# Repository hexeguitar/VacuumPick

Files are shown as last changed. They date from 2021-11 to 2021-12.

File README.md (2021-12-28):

# VacuumPick
### DIY vacuum pick up project for hand SMT assembly. 
The hardware is based around an inexpensive air pump, 3 valves and a controller board utilizing the ATTINY806 microcontroller.  
Firmware is available as PlatformIO project (sources) and a precompiled hex file.  
The enclosure and the handle was reused from a damaged Ayoue932 vacuum pick up.

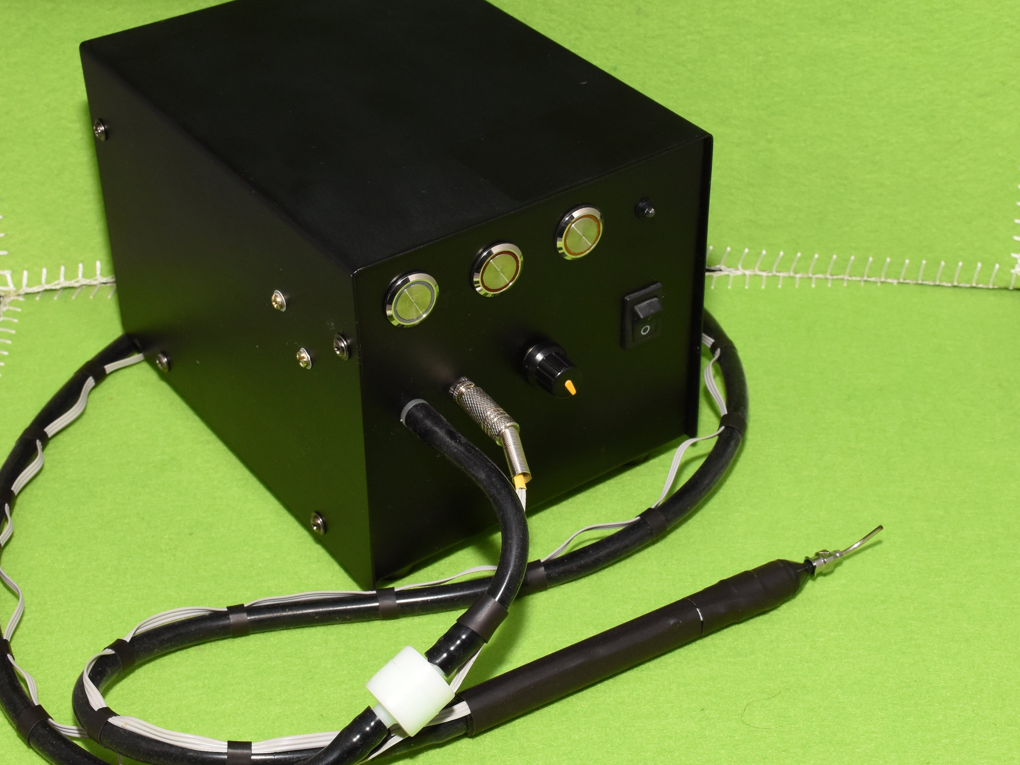
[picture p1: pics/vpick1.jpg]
  

--- 
### Operation
* vacuum activated using a touch button on the handle or a footswitch
*  Button 1: Vacuum mode
*  Button 2: Clean/air blow mode for cleaning the nozzle
*  Button 3: pump always on mode
*  0-100% pump speed control using a potentiometer


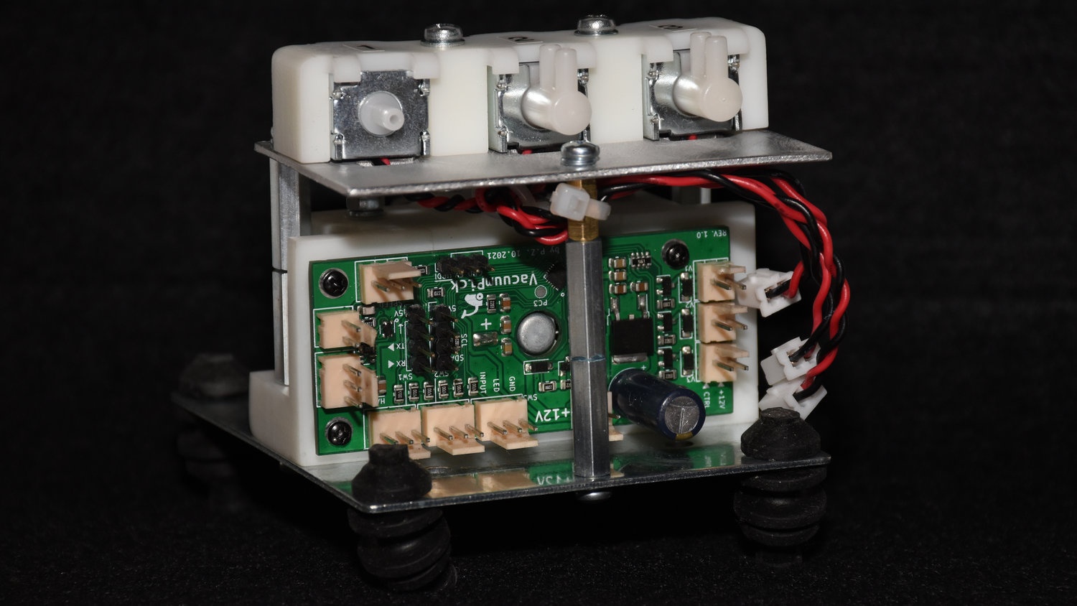
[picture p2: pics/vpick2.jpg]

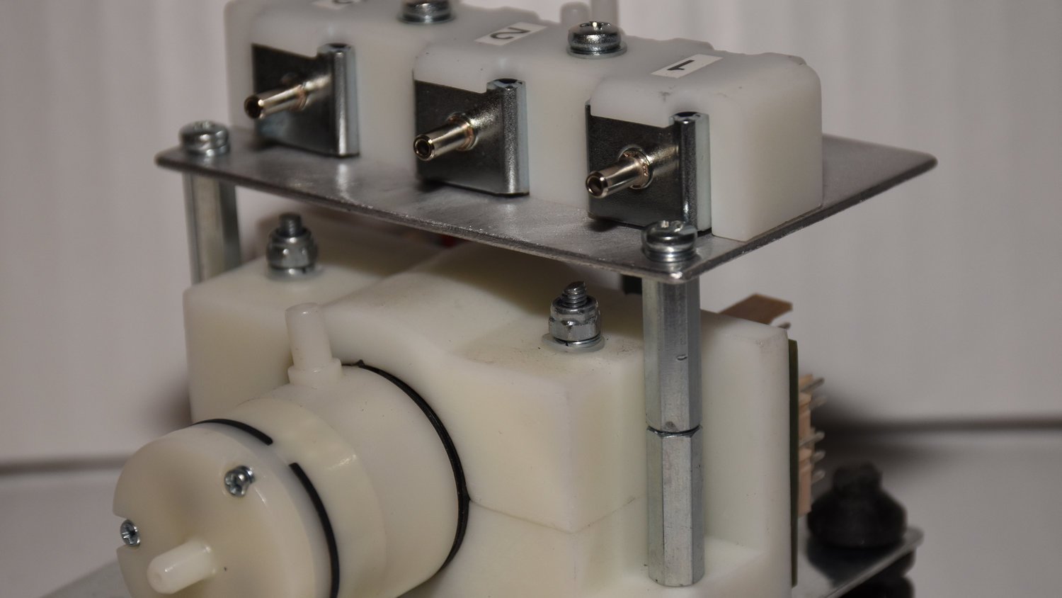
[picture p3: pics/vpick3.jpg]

   ___   
### Electronics  
* ATTINY806 MCU  
* 3 x open drain MOSFET outputs for valve controls
* 3 x illuminated button inputs
* Footswitch or handle button input (incl. 5V power for touch sensors)
* Pot input as motor speed control
* UART TX/RX for debugging purposes
* I2C header for future expansion
* UPDI programmer input
* 12V DC 1A input power requirement  

Board is designed in **KiCad 6.0**, available as project and generated gerber files.   
### [Schematic]

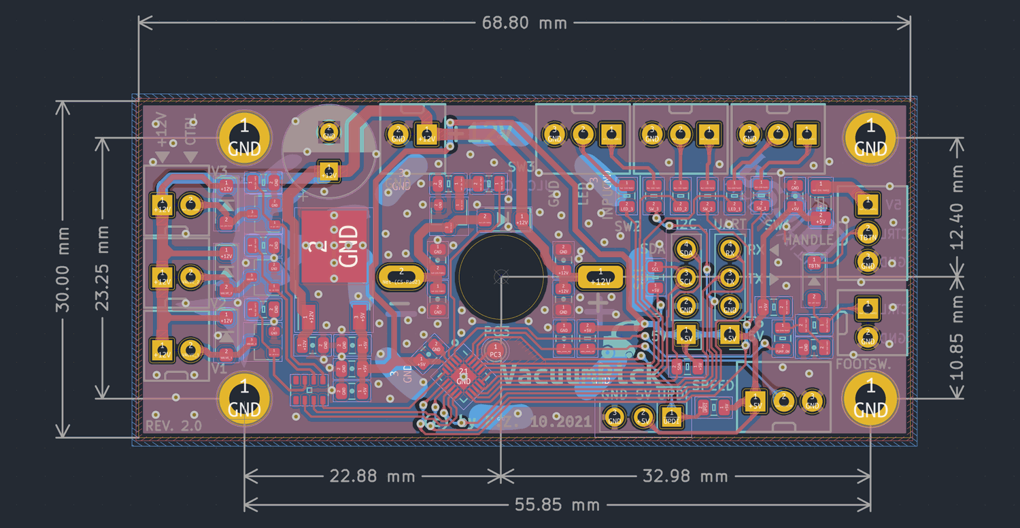
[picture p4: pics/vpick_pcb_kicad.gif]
  
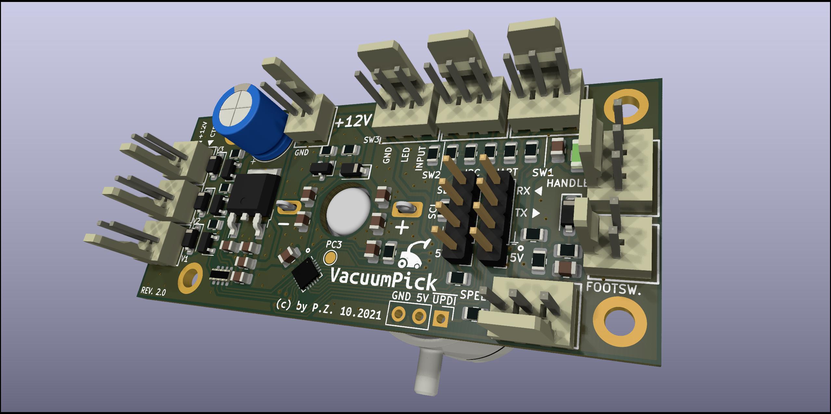
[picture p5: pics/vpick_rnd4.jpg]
  

   ---   
### Mechanical design  
Design is done using FreeCAD:  

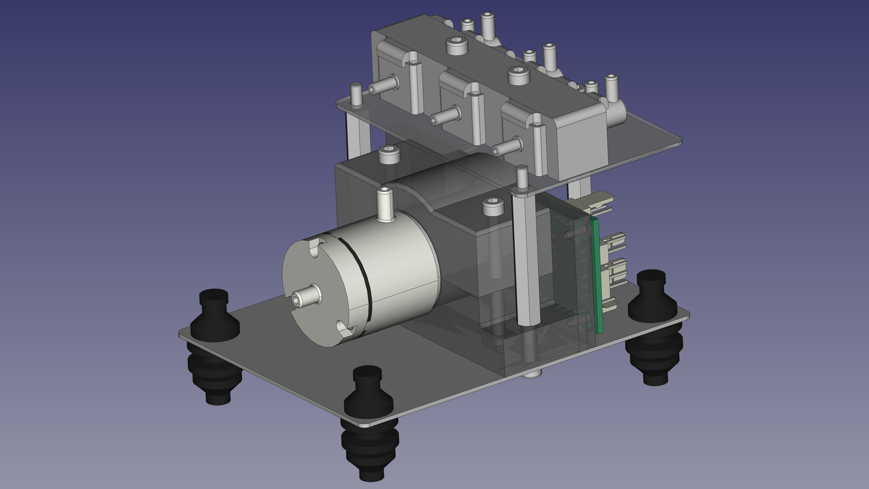
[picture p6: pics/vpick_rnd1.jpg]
      
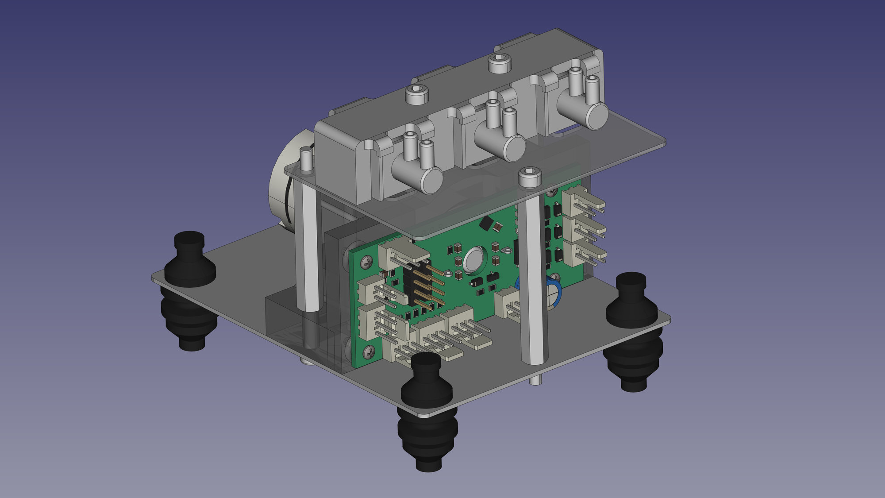
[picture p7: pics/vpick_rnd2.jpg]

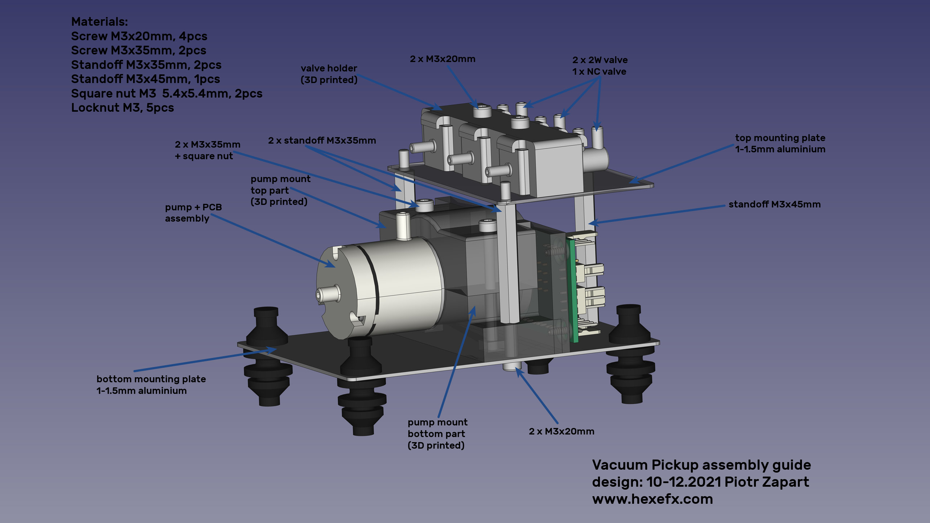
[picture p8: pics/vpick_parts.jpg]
 

The main parts are:  
* Base plate used to mount the pump holder and the rest of the assembly (see [MountingPlates])
* Top plate used to mount the valves
* 2 part 3D printed pump holder (step files are available)
* Valve holder - 3D printed part
* Various hardware: M3 standoffs, screws, locknuts, etc.  
 
---  
### System  

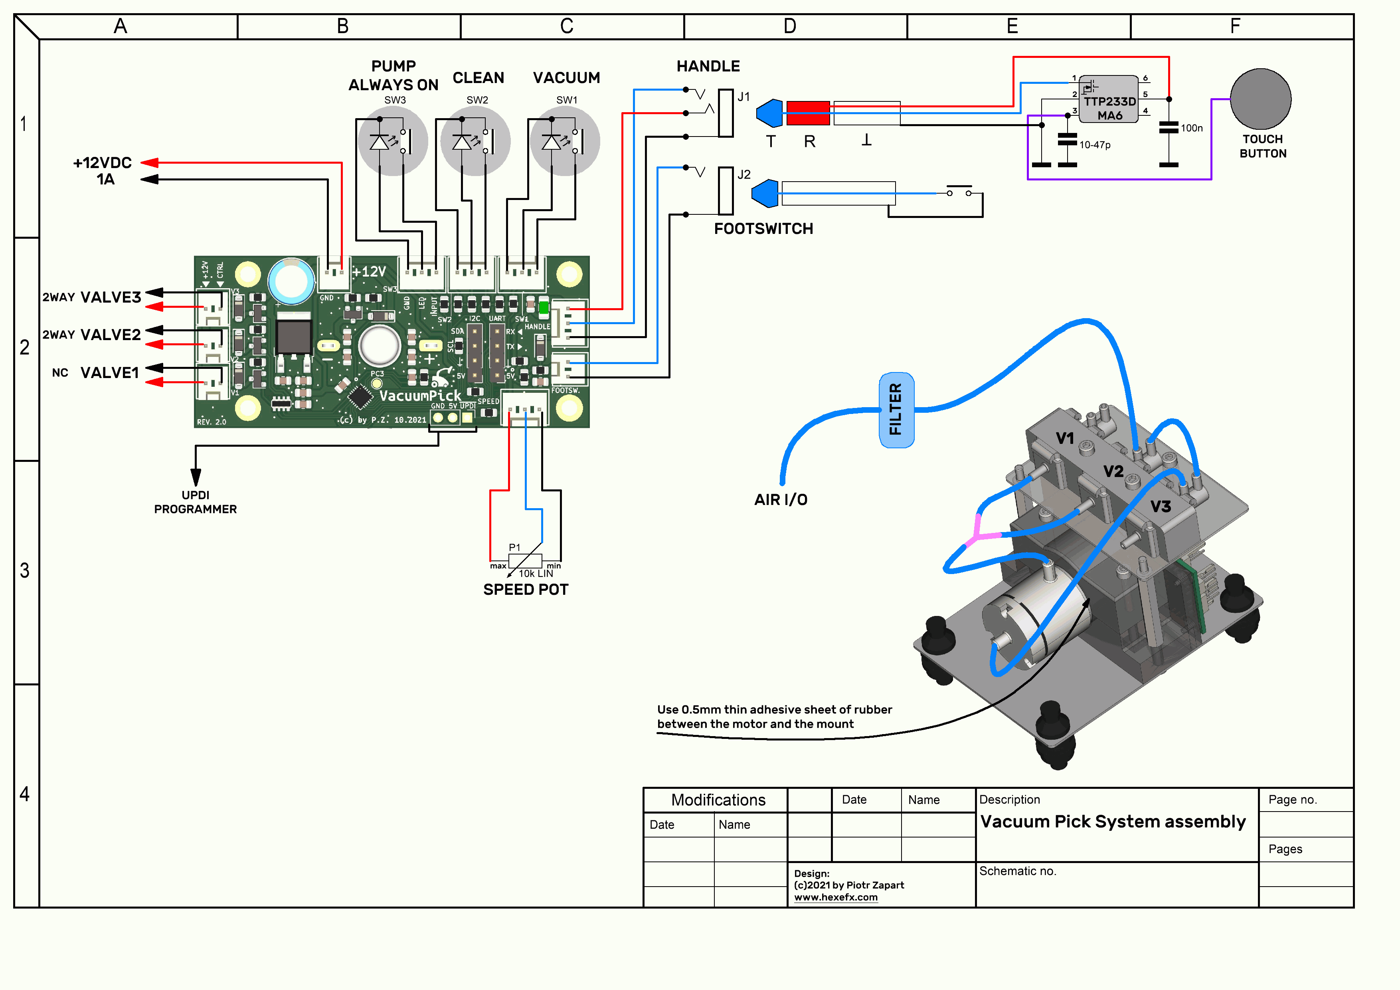
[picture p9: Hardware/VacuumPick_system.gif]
 

---  
### Handle  

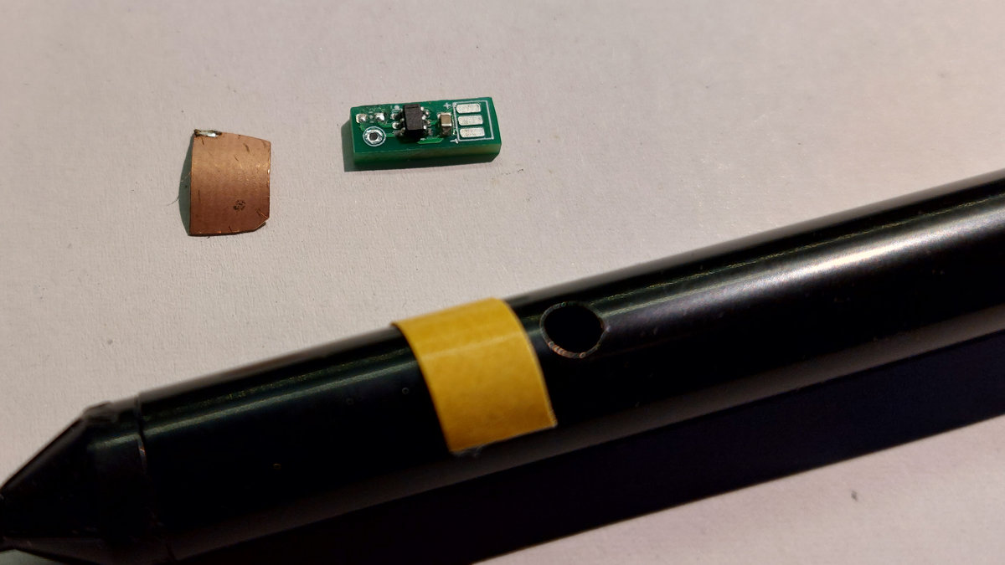
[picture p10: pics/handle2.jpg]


Pump can be controlled using either a footswitch or a button installed directly on the handle. The latter is my preferred method which i'm quite used to. I decided to install a capacitive touch button near the hole on the handle achieve two things:
* a slight move of the finger covering the hole enables the pump and increases the suction force
* to release the part all i need to do is to move the finger out of hole, this stops the pump and releases the part.  
  
The touch sensor is made of a piece of thin copper clad and uses the TTP223D-MA6 capacitive touch button IC. There are a few variants of the TTP223 chip, some having an option for open drain or push-pull output. The one i have has one control pin only (momentary/toggle operation) and an open drain output. The board is designed to work with this type of the output, so in case you are using a different model, make sure it's properly configured.  

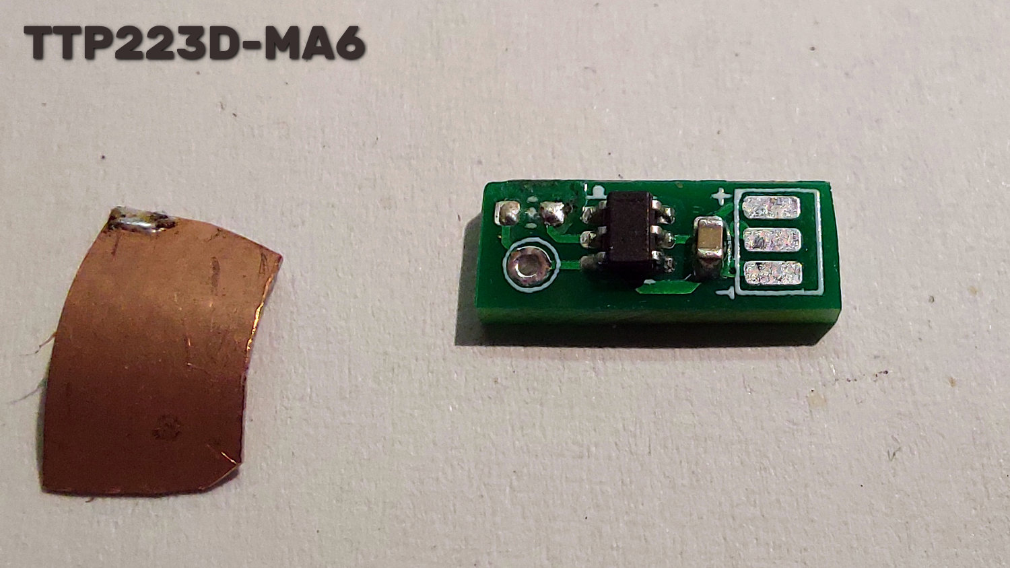
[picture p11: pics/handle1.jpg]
  

This is a small board i designed for the TTP223-MA6 chip. Important feature is the touch sensor sensitivity adjustment using a small 0 - 51pF 0603 capacitor placed in parallel with the input. Experiment with a value to get a desired button response. In my case (handle made of metal) i had to add a 47pf cap to make it work reliably. Otherwise even touching the handle would enable the pump.  

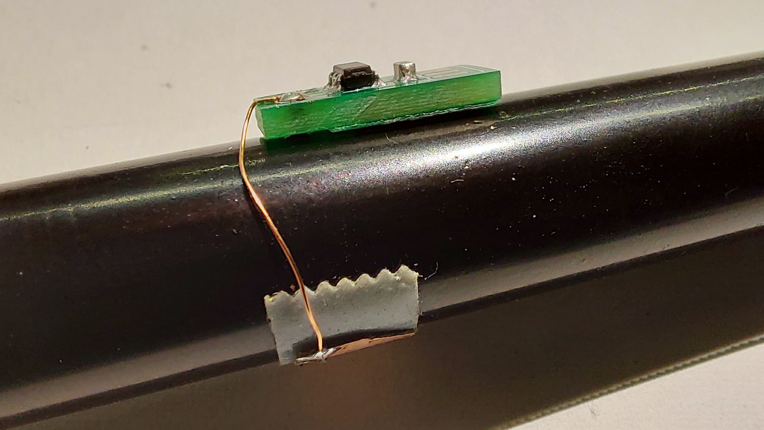
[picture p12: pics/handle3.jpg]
  

Once installed everything was secured using a heat shrink tube.  

--- 
VacuumPick in action:  

VacuumPick (http://www.youtube.com/watch?v=vpaEpUIYMoU)

----  
Copyright 2021 by Piotr Zapart  
www.hexefx.com

[pic1]: pics/vacuum3.jpg "VaccumPick"
[pic2]: pics/vpick_rnd4.jpg "VaccumPick"
[pic3]: pics/vpick_rnd1.jpg "VaccumPick"
[pic4]: pics/vpick_rnd2.jpg "VaccumPick"
[pic5]: pics/vpick_rnd3.jpg "VaccumPick"
[pic6]: pics/vpick_parts.jpg "VaccumPick"
[pic7]: pics/vpick_pcb_kicad.gif "VaccumPick"
[pic8]: pics/vpick1.jpg "VaccumPick"
[pic9]: pics/vpick2.jpg "VaccumPick"
[pic10]: pics/vpick3.jpg "VaccumPick"
[pic11]: pics/vpick4.jpg "VaccumPick"
[pic12]: Hardware/VacuumPick_system.gif "VaccumPick"
[pic13]: pics/handle1.jpg "VaccumPick-Handle"
[pic14]: pics/handle2.jpg "VaccumPick-Handle"
[pic15]: pics/handle3.jpg "VaccumPick-Handle"

[Schematic]: /Hardware/VacuumPick_schm.pdf "Schematic"
[MountingPlates]: /Hardware/VacuumPick_MountingPlates.pdf "Plates mech. drawings"

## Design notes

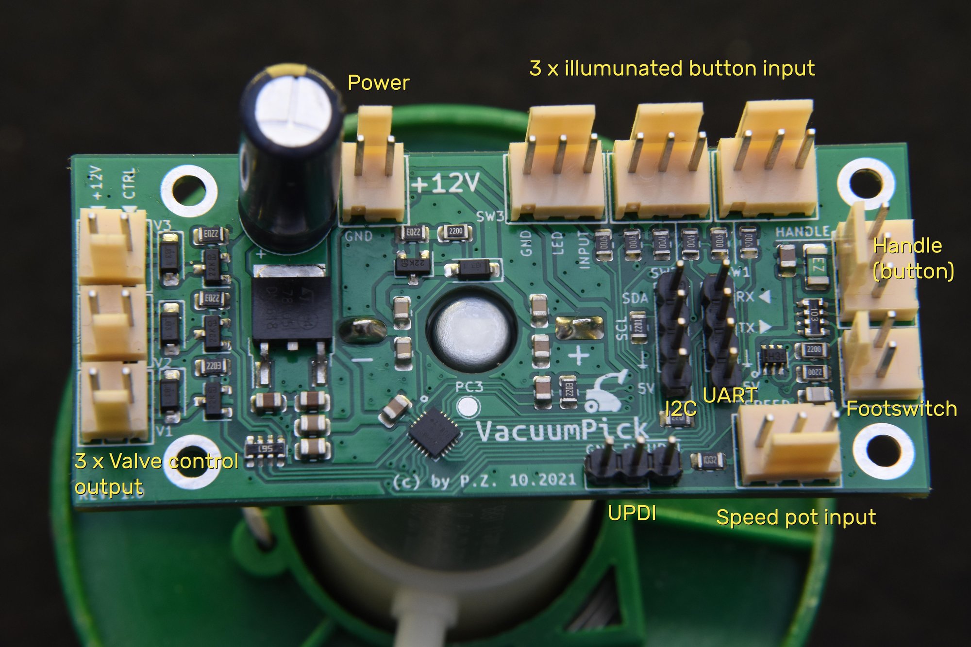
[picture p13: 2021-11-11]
pics/vacuum3.jpg

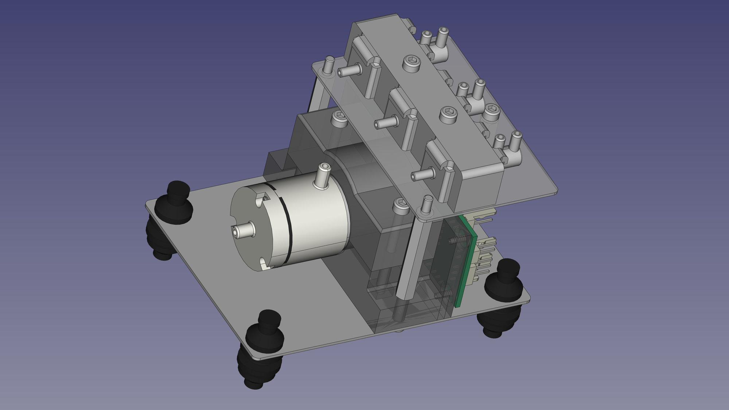
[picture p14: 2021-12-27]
pics/vpick_rnd3.jpg

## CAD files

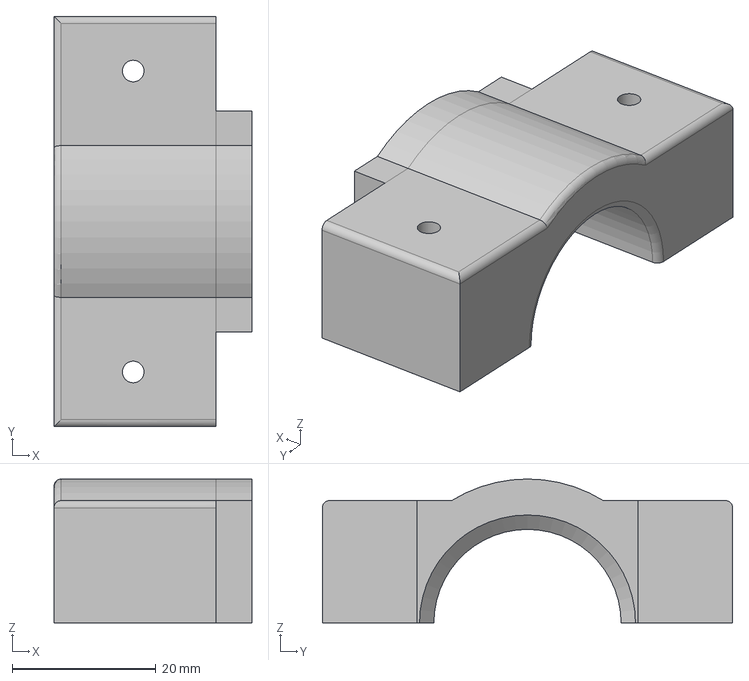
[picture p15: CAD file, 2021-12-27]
Hardware/3d/pump_mount_top.step
27.5 x 57.0 x 20.0 mm

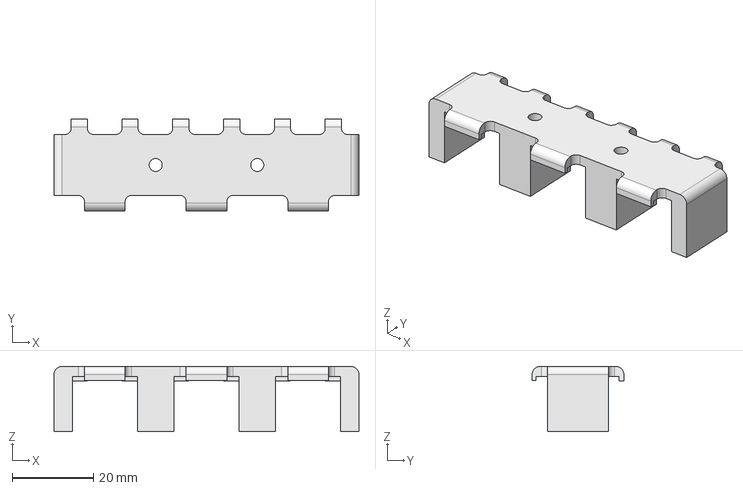
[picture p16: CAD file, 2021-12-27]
Hardware/3d/valve_holder.step
75.0 x 22.6 x 16.0 mm

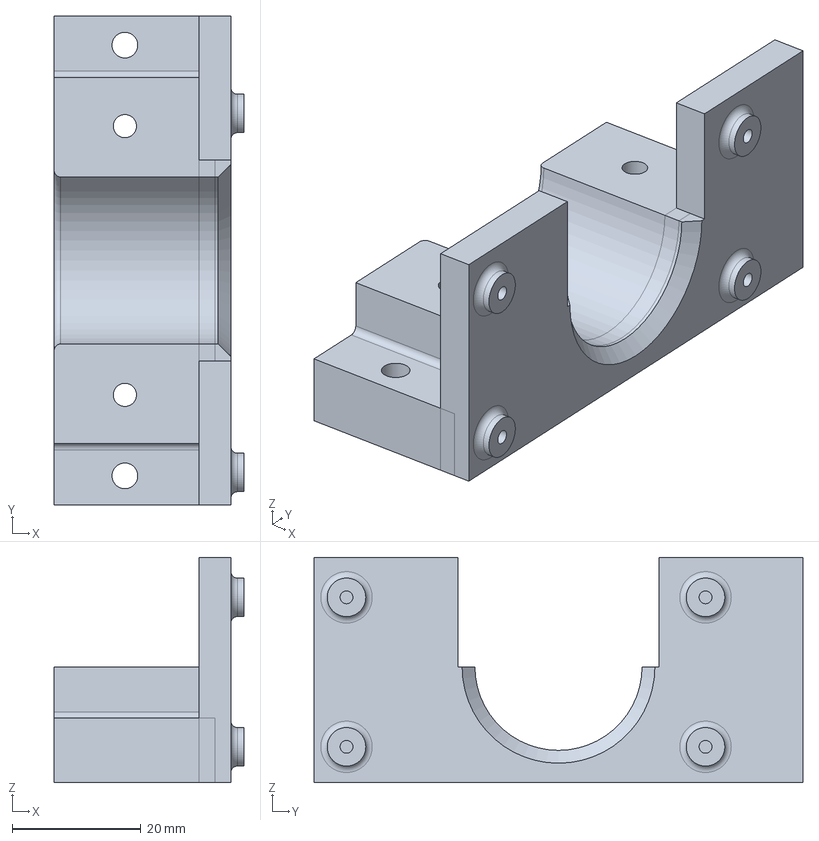
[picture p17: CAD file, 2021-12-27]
Hardware/3d/pump_mount_base.step
29.5 x 76.0 x 35.0 mm

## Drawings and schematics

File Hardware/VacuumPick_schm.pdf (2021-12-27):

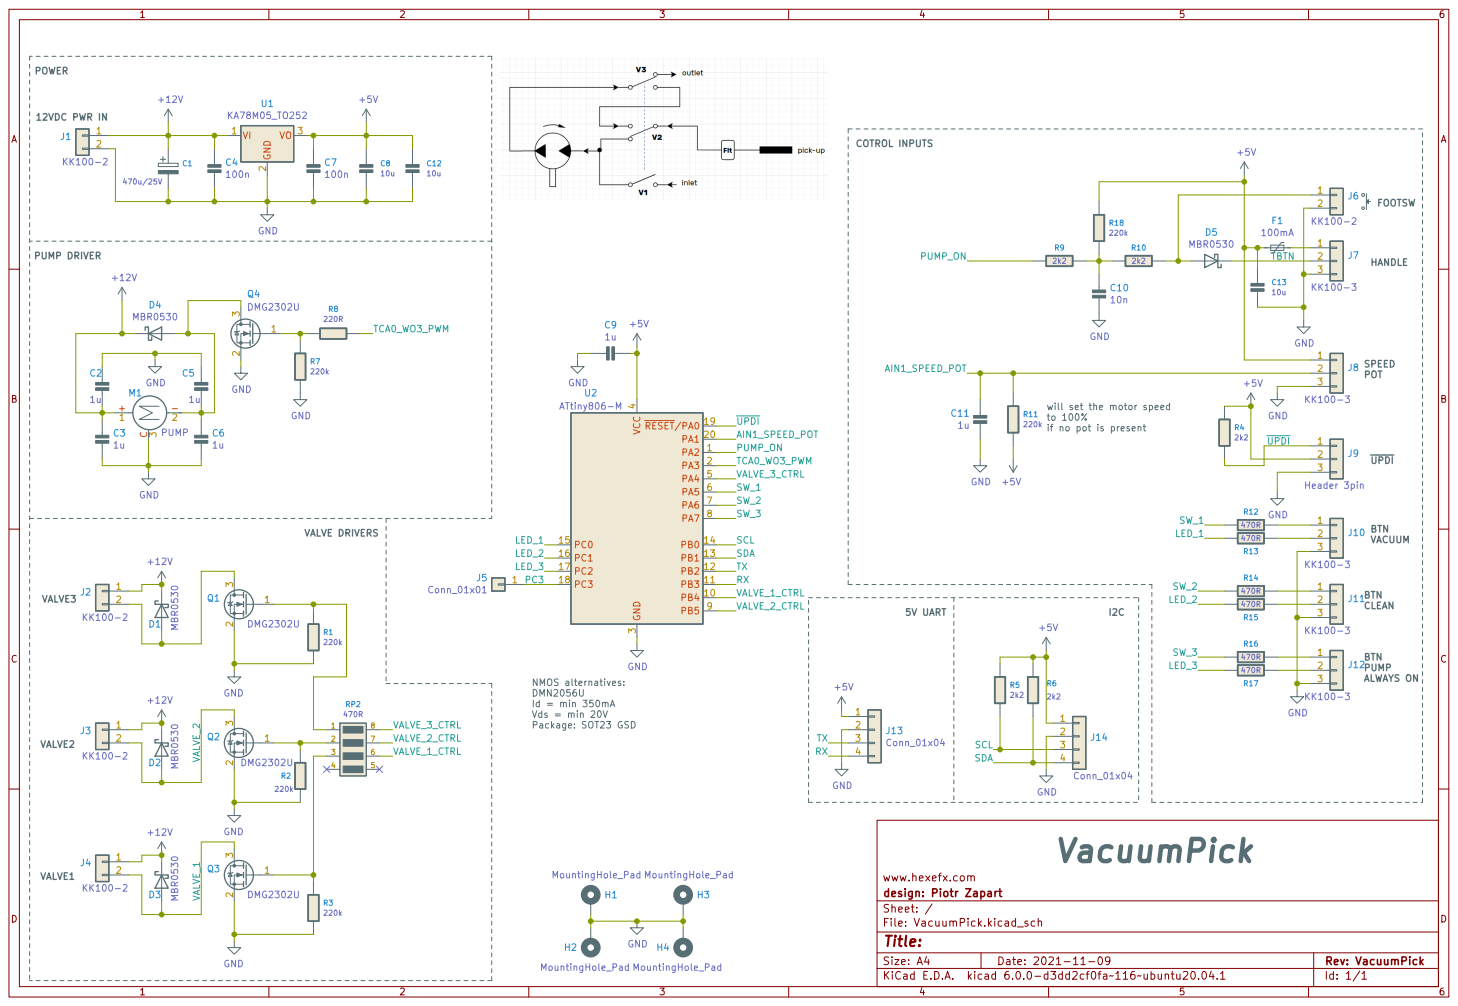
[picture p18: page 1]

POWER

PUMP DRIVER

will set the motor speed
1u GND
~{UPDI} SDA

if no pot is present VALVE3 VALVE2 VALVE1

File: VacuumPick.kicad_sch Sheet: / design: Piotr Zapart www.hexefx.com

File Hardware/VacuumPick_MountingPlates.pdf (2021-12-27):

4

x

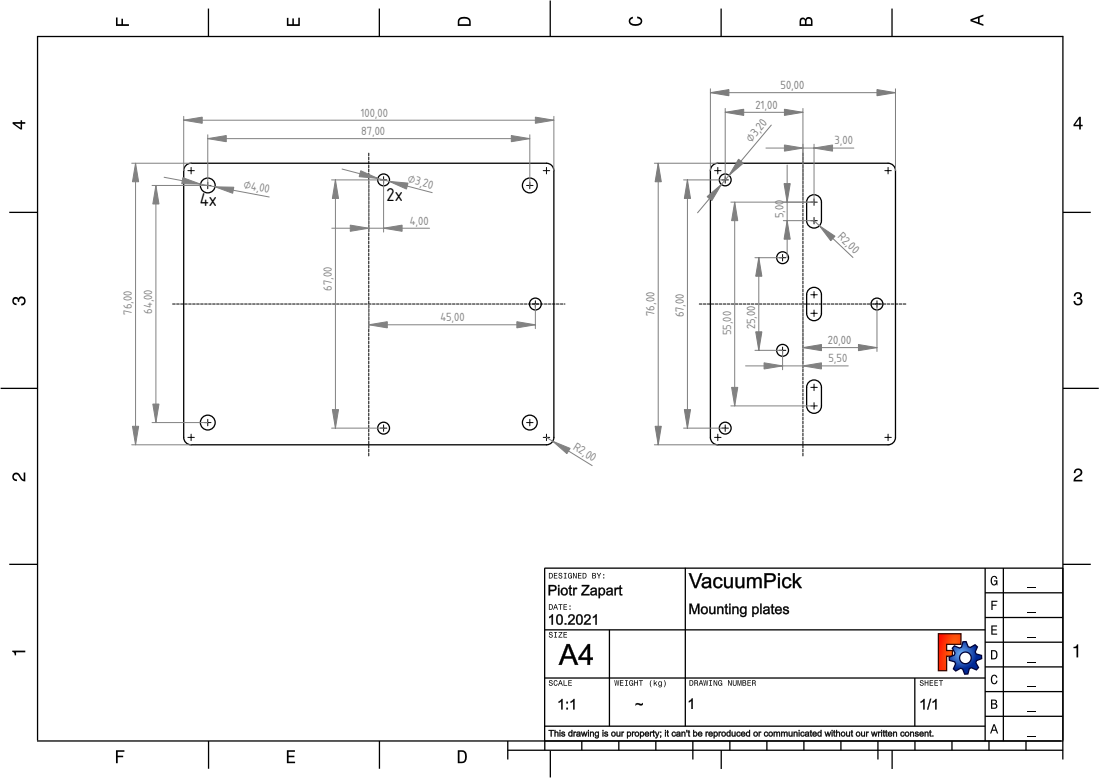
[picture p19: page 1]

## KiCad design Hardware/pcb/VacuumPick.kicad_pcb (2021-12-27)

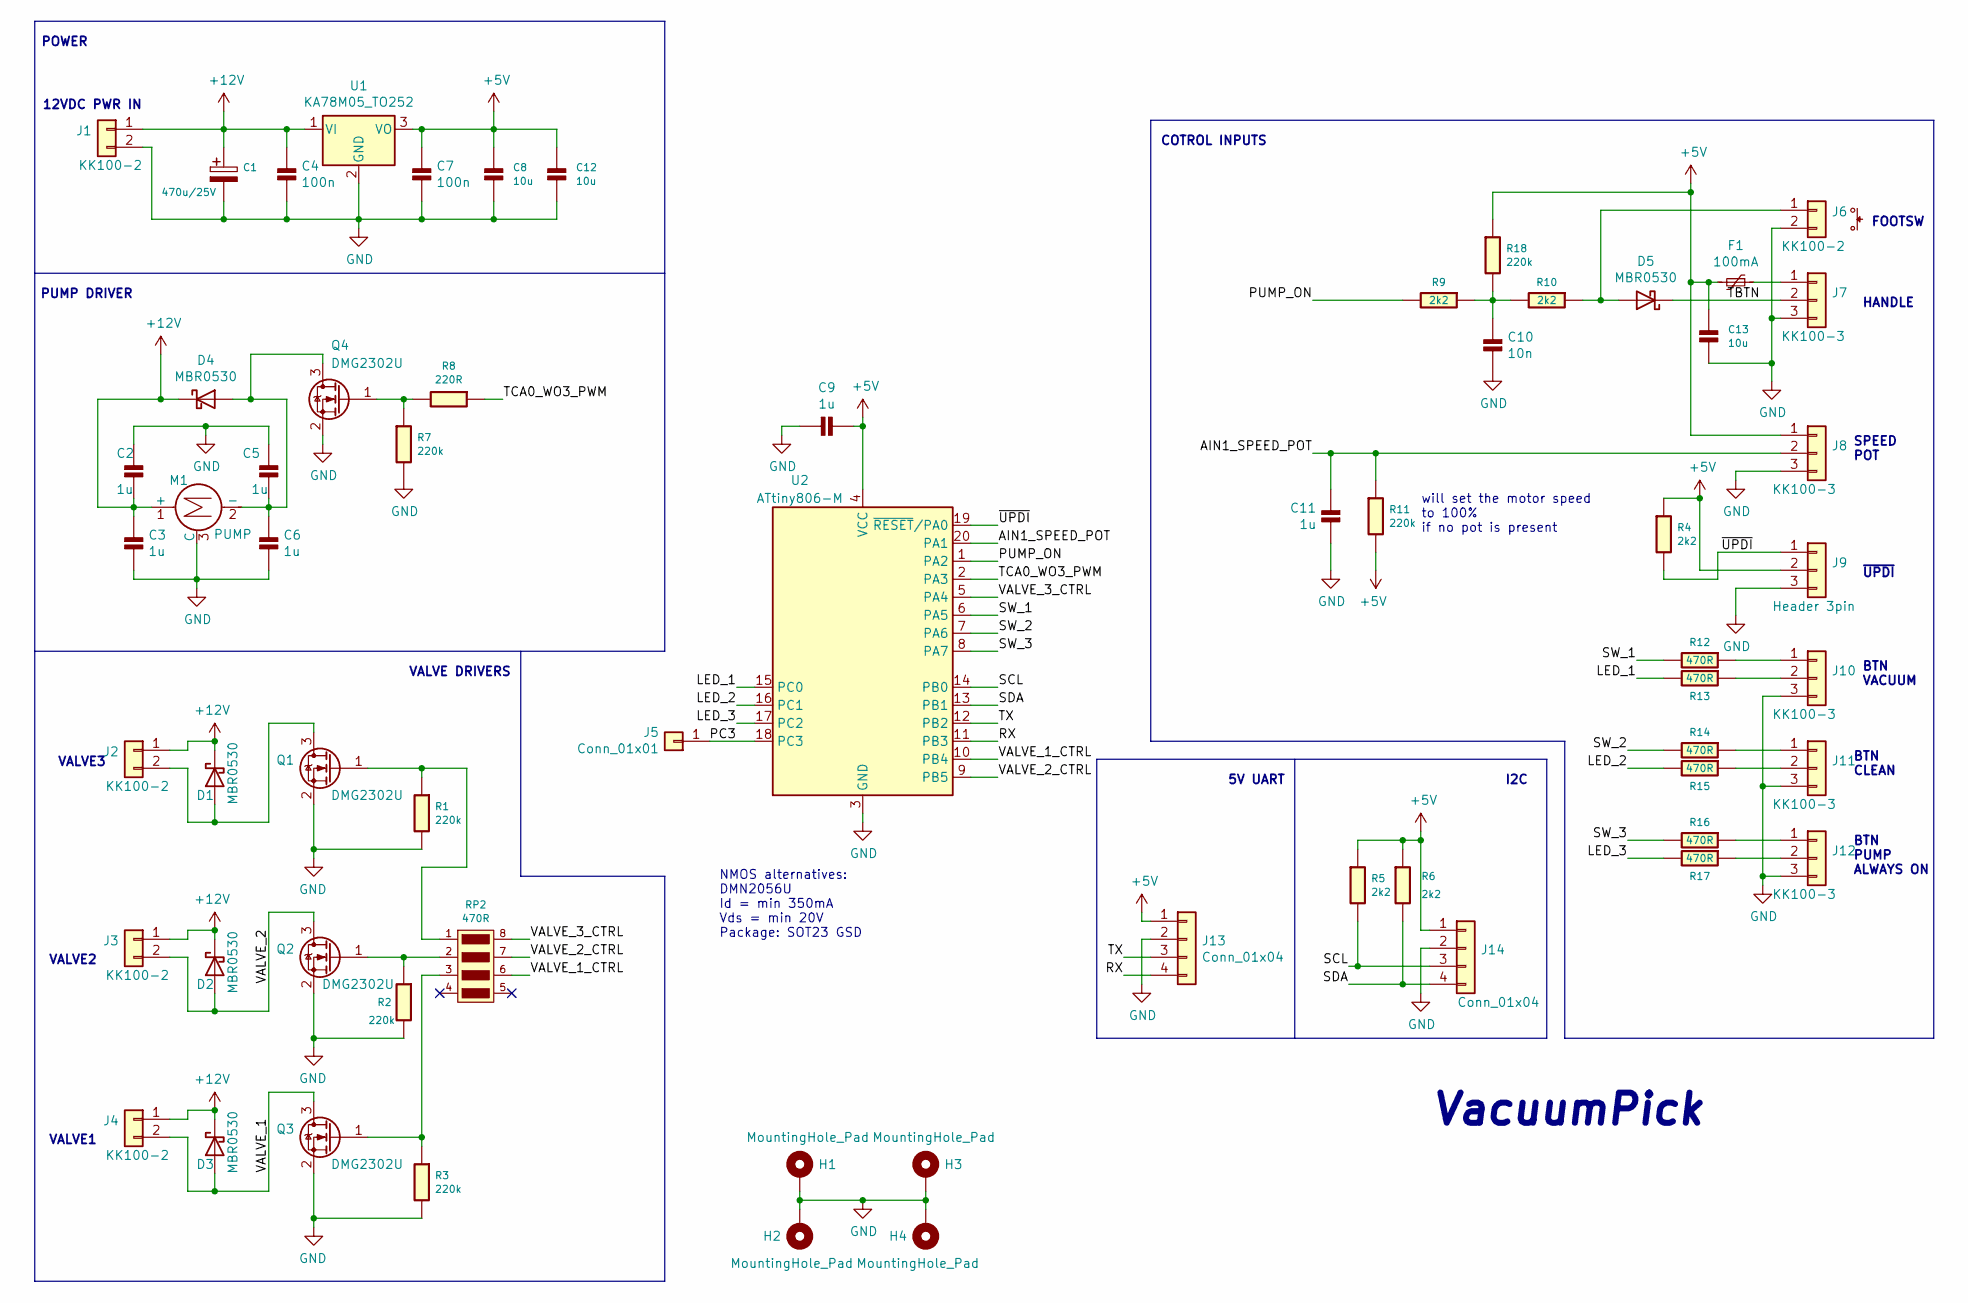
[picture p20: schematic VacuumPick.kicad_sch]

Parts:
C1: 470u/25V; CP_Radial_D8.0mm_P3.50mm
C2, C3, C5, C6, C9, C11: 1u; Hx_C_0805_2012Metric
C4, C7: 100n; Hx_C_0805_2012Metric
C8, C12, C13: 10u; Hx_C_0805_2012Metric
C10: 10n; Hx_C_0805_2012Metric
D1, D2, D3, D4, D5: MBR0530; D_SOD-123
F1: 100mA; Fuse_1206_3216Metric
H1: MountingHole_Pad; MountingHole_2.7mm_M2.5_DIN965_Pad
H2, H3, H4: MountingHole_Pad; MountingHole_2.7mm_M2.5_ISO7380_Pad
J1, J2, J3, J4, J6: KK100-2; 1x2_254_socket_H
J5: Conn_01x01; TestPoint_Pad_D1.5mm
J7, J8, J10, J11, J12: KK100-3; 1x3_254_socket_H
J9: Header 3pin; PinHeader_1x03_P2.54mm_Vertical
J13, J14: Conn_01x04; PinHeader_1x04_P2.54mm_Vertical
M1: PUMP; VacuumPump_DC12V
Q1, Q2, Q3, Q4: DMG2302U; SOT-23
R1, R2, R3, R7, R11, R18: 220k; Hx_R_0805_2012Metric
R4, R5, R6, R9, R10: 2k2; Hx_R_0805_2012Metric
R8: 220R; Hx_R_0805_2012Metric
R12, R13, R14, R15, R16, R17: 470R; Hx_R_0805_2012Metric
RP2: 470R; R_Array_Convex_4x0603
U1: KA78M05_TO252; TO-252-2
U2: ATtiny806-M; VQFN-20-1EP_3x3mm_P0.4mm_EP1.7x1.7mm

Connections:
+5V: C7.1, C8.1, C9.1, C12.1, C13.1, F1.2, J8.1, J9.2, J13.1, J14.1, R4.1, R5.1, R6.1, R11.2, R18.1, U1.3 (VO), U2.4 (VCC)
+12V: C1.1, C2.2, C3.1, C4.1, D1.1 (K), D2.1 (K), D3.1 (K), D4.1 (K), J1.1, J2.1, J3.1, J4.1, M1.1 (+), U1.1 (VI)
/AIN1_SPEED_POT: C11.2, J8.2, R11.1, U2.20 (PA1)
/LED_1: R13.2, U2.15 (PC0)
/LED_2: R15.2, U2.16 (PC1)
/LED_3: R17.2, U2.17 (PC2)
/PC3: J5.1, U2.18 (PC3)
/PUMP_ON: R9.2, U2.1 (PA2)
/RX: J13.4, U2.11 (PB3)
/SCL: J14.3, R5.2, U2.14 (PB0)
/SDA: J14.4, R6.2, U2.13 (PB1)
/SW_1: R12.2, U2.6 (PA5)
/SW_2: R14.2, U2.7 (PA6)
/SW_3: R16.2, U2.8 (PA7)
/TBTN: D5.1 (K), J7.2
/TCA0_WO3_PWM: R8.1, U2.2 (PA3)
/TX: J13.3, U2.12 (PB2)
/VALVE_1: D3.2 (A), J4.2, Q3.3 (D)
/VALVE_1_CTRL: RP2.6 (R3), U2.10 (PB4)
/VALVE_2: D2.2 (A), J3.2, Q2.3 (D)
/VALVE_2_CTRL: RP2.7 (R2), U2.9 (PB5)
/VALVE_3_CTRL: RP2.8 (R1), U2.5 (PA4)
/~UPDI: J9.1, R4.2, U2.19 (~RESET/PA0)
GND: C1.2, C2.1, C3.2, C4.2, C5.1, C6.2, C7.2, C8.2, C9.2, C10.1, C11.1, C12.2, C13.2, H1.1, H2.1, H3.1, H4.1, J1.2, J6.2, J7.3, J8.3, J9.3, J10.3, J11.3, J12.3, J13.2, J14.2, M1.3 (C), Q1.2 (S), Q2.2 (S), Q3.2 (S), Q4.2 (S), R1.2, R2.2, R3.2, R7.2, U1.2 (GND), U2.3 (GND), U2.21 (GND)
unnamed: C5.2, C6.1, D4.2 (A), M1.2 (-), Q4.3 (D)
unnamed: C10.2, R9.1, R10.2, R18.2
unnamed: D1.2 (A), J2.2, Q1.3 (D)
unnamed: D5.2 (A), J6.1, R10.1
unnamed: F1.1, J7.1
unnamed: J10.1, R12.1
unnamed: J10.2, R13.1
unnamed: J11.1, R14.1
unnamed: J11.2, R15.1
unnamed: J12.1, R16.1
unnamed: J12.2, R17.1
unnamed: Q1.1 (G), R1.1, RP2.1
unnamed: Q2.1 (G), R2.1, RP2.2
unnamed: Q3.1 (G), R3.1, RP2.3
unnamed: Q4.1 (G), R7.1, R8.2

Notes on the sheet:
BTN VACUUM
~{UPDI}
PUMP DRIVER
5V UART
VALVE DRIVERS
BTN PUMP ALWAYS ON
FOOTSW
VALVE3
I2C
SPEED POT
NMOS alternatives: DMN2056U Id = min 350mA Vds = min 20V Package: SOT23 GSD
VacuumPick
VALVE2
BTN CLEAN
12VDC PWR IN
COTROL INPUTS
VALVE1
POWER
will set the motor speed to 100% if no pot is present
HANDLE

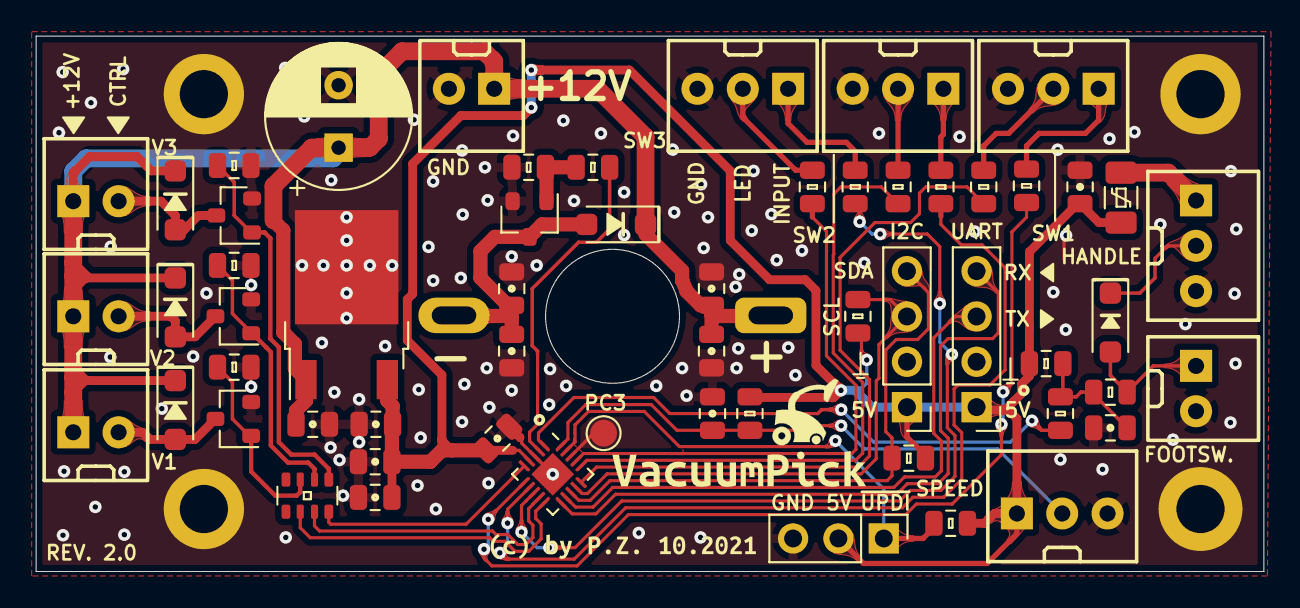
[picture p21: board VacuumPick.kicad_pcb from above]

Board: 2 copper layers, 68.8 x 30.0 mm, 65 parts (0 on the bottom side), 39 nets.

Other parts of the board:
kibuzzard-61600490, kibuzzard-61600814: G***; label

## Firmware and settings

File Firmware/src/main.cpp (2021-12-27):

/*
 * Copyright (c) 2021 by Piotr Zapart / www.hexefx.com
 *
 * All rights reserved.
 *
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
 * Neither the name of the Piotr Zapart or HEXE FX nor the names of its 
 * contributors may be used to endorse or promote products derived from this software 
 * without specific prior written permission.
 * 
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
 */
#include <Arduino.h>
#include "button.h"
#include "Wire.h"
#include "pump.h"
#include "valve.h"

// pin definiions 
#define POT_PIN     PIN_PA1

#define V1_PIN      PIN_PB4
#define V2_PIN      PIN_PB5
#define V3_PIN      PIN_PA4

#define LED1_PIN    PIN_PC0
#define LED2_PIN    PIN_PC1
#define LED3_PIN    PIN_PC2

#define PUMP_PIN    PIN_PA3

uint8_t speed = 0, speed_old = 0;

ValveSystem valves(V1_PIN, V2_PIN, V3_PIN);
Pump pump(PUMP_PIN);

void setup()
{
    //Serial.begin(115200);
    //Serial.println(F("VacuumPick"));
    pump.init();
    pinMode(LED1_PIN, OUTPUT); digitalWrite(LED1_PIN, HIGH);
    pinMode(LED2_PIN, OUTPUT); digitalWrite(LED2_PIN, LOW);
    pinMode(LED3_PIN, OUTPUT); digitalWrite(LED3_PIN, LOW);

    btn_init();
    analogReadResolution(8);
}

void loop()
{
    speed = analogRead(POT_PIN);
    if (speed != speed_old)
    {
        pump.setSpeed(speed);
        speed_old = speed;
    }

    if (btn_get_press(1<<BTN1))
    {
        valves.set(VALVE_MODE_VACUUM);
        digitalWriteFast(LED1_PIN, HIGH);
        digitalWriteFast(LED2_PIN, LOW);
    }
    if (btn_get_press(1<<BTN2))
    {
        valves.set(VALVE_MODE_BLOW);
        digitalWriteFast(LED1_PIN, LOW);
        digitalWriteFast(LED2_PIN, HIGH);
    }
    if (btn_get_press(1<<BTN3))
    {
        bool result = pump.toogleAlwaysOn();
        digitalWrite(LED3_PIN, result);
    }
    if (btn_get_press(1<<PUMP_EN))
    {
        pump.on();
    }
    if (btn_get_release(1<<PUMP_EN))
    {
        pump.off();
    }
    if (btn_get_long(1<<PUMP_EN))
    {
        Serial.println(F("Pump LONG"));
    }

    pump.update();
}

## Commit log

2021-12-27 major update
    [VacuumPick-B_Cu.gbr, VacuumPick-B_Mask.gbr, VacuumPick-B_SilkS.gbr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]
2021-12-27 missing files
    [VacuumPick.kicad_pcb, VacuumPick.kicad_sch, pump_mount_base.step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]
